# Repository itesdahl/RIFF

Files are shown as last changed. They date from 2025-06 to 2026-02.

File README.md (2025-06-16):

# The RIFF 600/900 DIY 3D printer
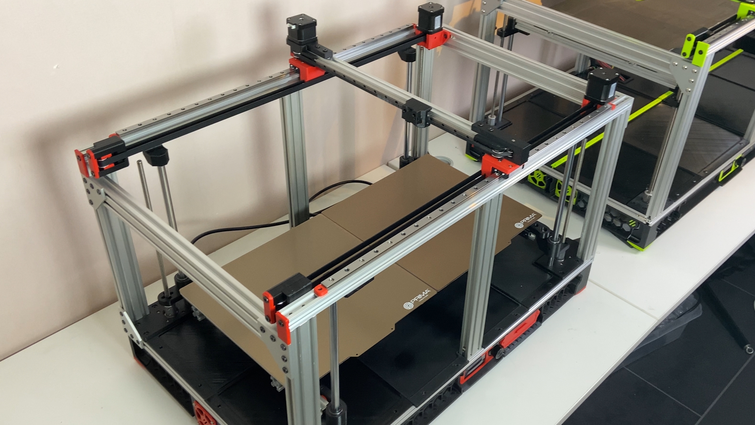
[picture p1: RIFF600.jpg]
CRIFF 600


You'll find the Youtube build series about the RIFF 600 here https://www.youtube.com/playlist?list=PLHk1C7nPAl80ZWU28OD7yWof3j6T3yG72  
You can also find the published STLs on: https://www.printables.com/model/1291703-the-riff-large-3d-printer

This is a 300x600 (RIFF 600) or 300x900 (RIFF 900) size DIY printer that can be built without spending a fortune. 

I encourage the use of second hand parts and will not provide any complete BOM (listing specific new components/brands). 

The prototype/PoC for the RIFF series is the LemonBreeze. That printer is not as space efficient as the RIFF printers: https://www.youtube.com/playlist?list=PLHk1C7nPAl83ME56pqZpkaPyZSMLXAlih

> [!NOTE]
> Future plans for this project is to add the Bondtech Indx. It should be a good fit for this frame, for printing signs etc..

## Some key information about my original RIFF 600 build:

- Build plate 300 x 600 (assembly with 2 pcs 300x300 heat beds in the RIFF 600, 3 pcs in the RIFF 900) 
- 2020 and 2040 extrusions 
- SKR 1.4 turbo and SKR Pico controllerboards (use whatever you have that have enough drivers and can run Klipper)
- Radxa Rock 3C SBC (or a Pi. SBC with 3-4 USB ports recommended)
- MGN 12H rails/carriage on Y and X. (350mm on X and 2x650 RIFF 600 or 2x950mm RIFF 900 on Y)
- 12mm rods and bearings on Z 
- Cartesian (the belts are a bit too long for corexy) 
- Klipper firmware 
- Dual Y steppermotors
- Sensorless homing on X and Y 
- Dragonburner with Sherpa micro 
- 2 x 360W 24V power supplies (3 x 360 24V in the 900 version)

## Video part 1:

### Cutting extrusions 600/900:

- 4x2020 775mm for Y (or 1075mm for the 900 version)
- 2x2020 450mm and 2x2040 450mm for X
- 6x2040 340mm for Z (or optionally 370mm)

### Blind joints and corner plates plates:

Tap M5 holes in all 6 2040 Z extrusions (or minimum 4 of them as shown in the video)
Tap M5 holes in the top Y extrusion at least in one end. (The one facing the rear of the printer) 
Optional but recommended, tap Y-extrusions in both ends to provide for two extra sets of corner plates and a couple of cover plates
Drill access holes in all Y-extrusions to get to the button head screws in the Z-extrusions
Attach the front and rear corner plates. The front 2040 x extrusion should sit 40mm below the top of the Y-extrusion

>[!TIP]
>Check the frame for squareness and adjust/correct  as needed.
>Mount the 4 z-motor mounts with M5 10mm bolts. The motor mounts makes the frame more rigid. Check the frame again for squareness.

# Video part 2
Parts for the front and rear arms (heat bed sub assembly): 

- Front 1x366mm 2020 extrusion and 2x625 bearings

- Rear 1x322mm 2020 extrusion

# Video part 3
- The 2020 extrusion for the x axis is 440mm

> [!CAUTION]
> On my 600 build the 2020 extrusions for the bed assembly is 2 pcs 645mm. You have to check the bed mounts on your heat bed to determine if you need longer extrusions.

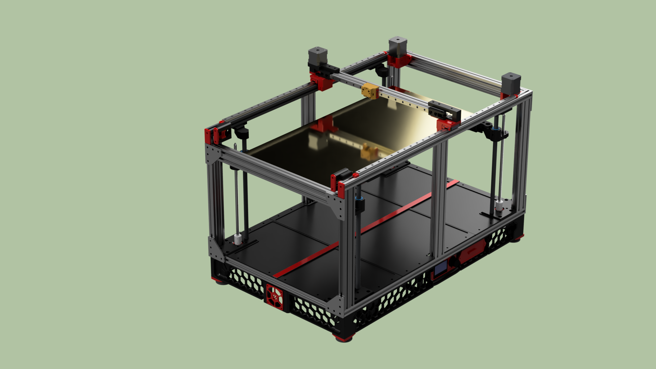
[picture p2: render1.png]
CAD model


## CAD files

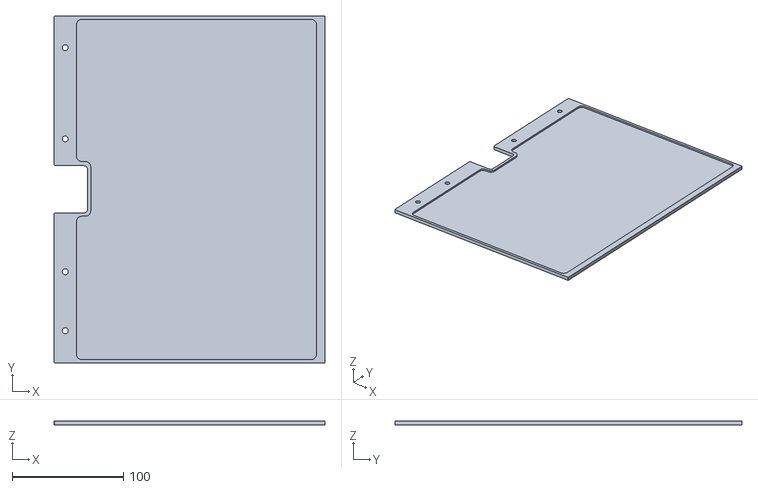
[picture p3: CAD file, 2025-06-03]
covers_skirt/mid_cover_left.stl
243.5 x 312.0 x 3.90

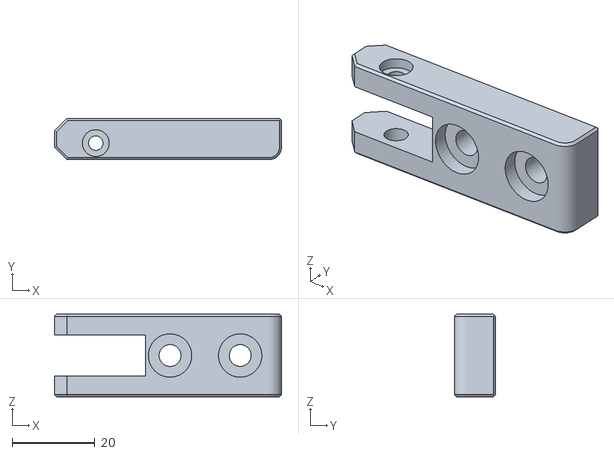
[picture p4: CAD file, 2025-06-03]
gantry/xoffset_motorside.stl
55.0 x 10.0 x 20.0

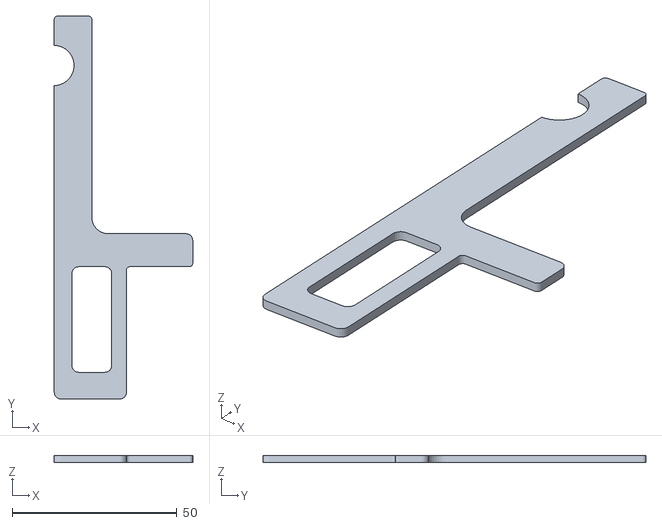
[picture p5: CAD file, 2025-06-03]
tools/jig_zrod_distance.stl
42.0 x 116.1 x 2.00

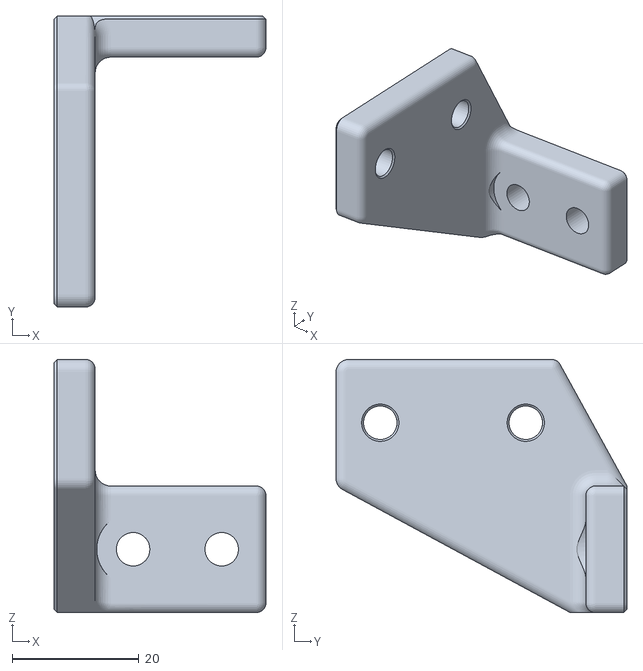
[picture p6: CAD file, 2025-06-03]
zaxis/2xbedbracketB.stl
33.5 x 46.0 x 40.0

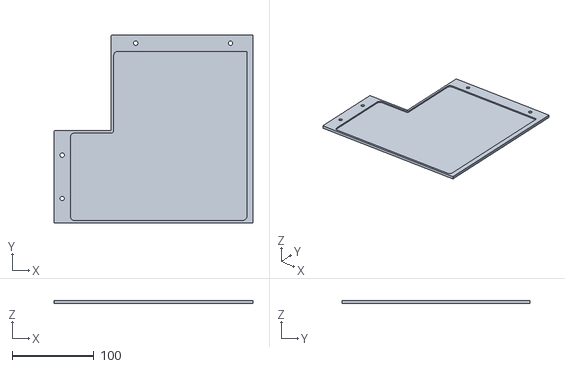
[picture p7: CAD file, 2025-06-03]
covers_skirt/rear_cover_left.stl
243.5 x 230.0 x 4.00

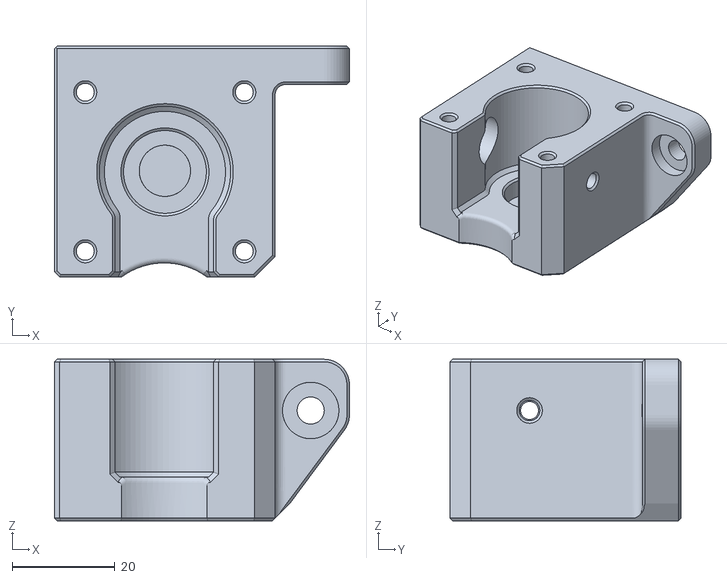
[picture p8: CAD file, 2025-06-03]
gantry/ymotor_mount_left.stl
57.5 x 45.0 x 31.5

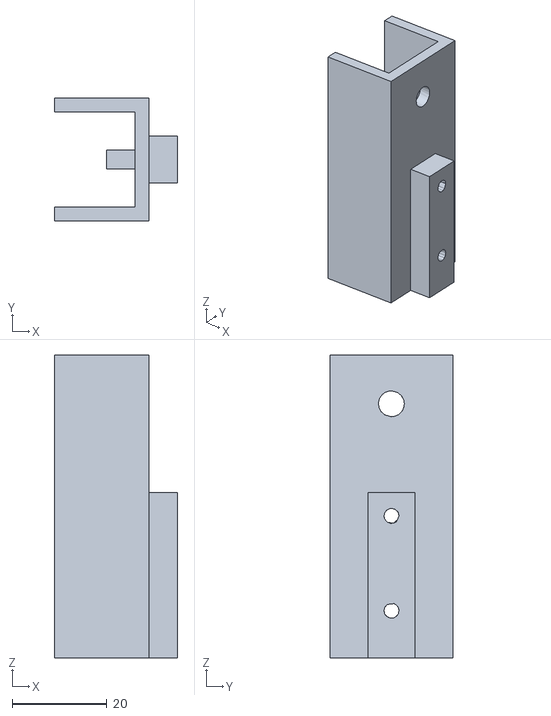
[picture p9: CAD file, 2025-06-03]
tools/jig_pilotholes.stl
26.0 x 26.0 x 64.0

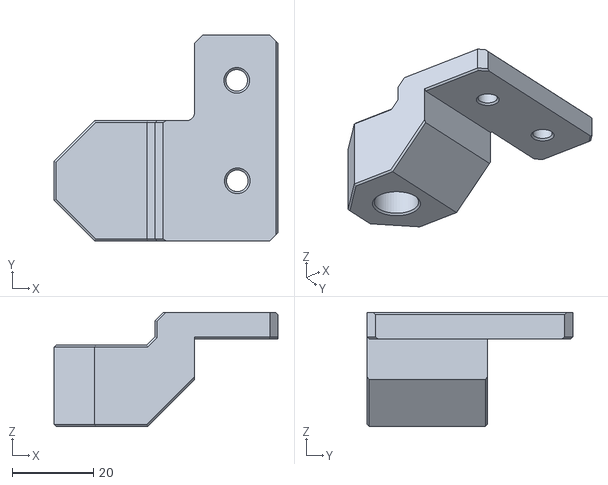
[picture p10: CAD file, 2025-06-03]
zaxis/2xzrod_mountA.stl
55.0 x 50.5 x 28.0

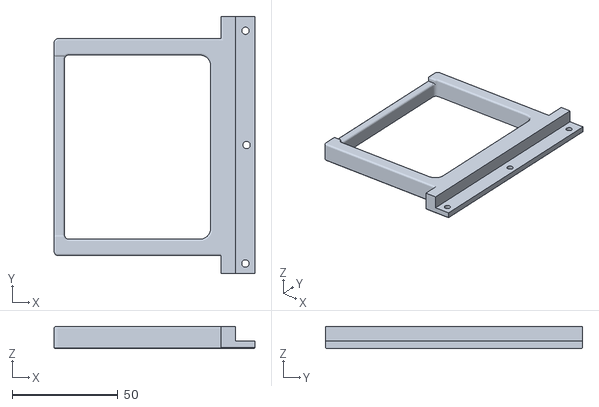
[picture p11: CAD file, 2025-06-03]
covers_skirt/caddy_supportbracket.stl
95.0 x 121.6 x 10.5

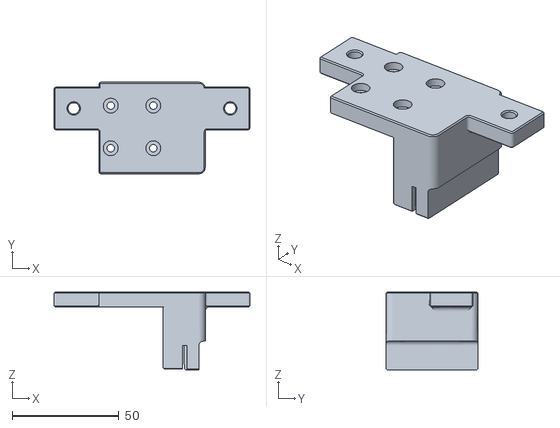
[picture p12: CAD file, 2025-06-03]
gantry/xyjoiner_left.stl
92.0 x 43.0 x 36.5

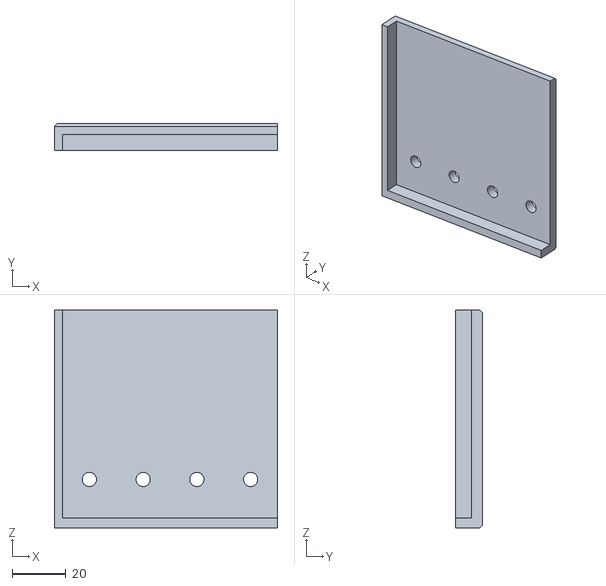
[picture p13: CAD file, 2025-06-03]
tools/jig_linup_extrusions.stl
83.0 x 10.0 x 81.0

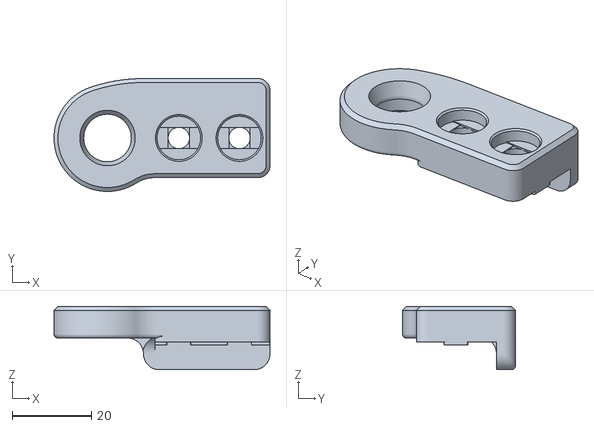
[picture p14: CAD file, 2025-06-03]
zaxis/left_spherical_left.stl
54.5 x 28.5 x 16.0

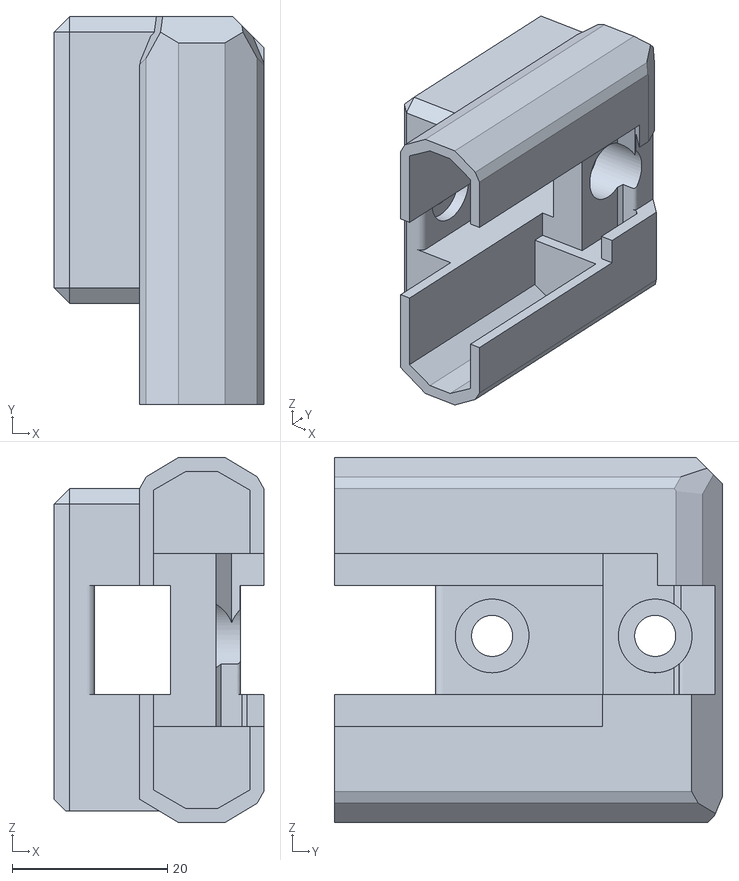
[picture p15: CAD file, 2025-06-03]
gantry/bfi_housing_left.stl
27.0 x 50.0 x 47.0

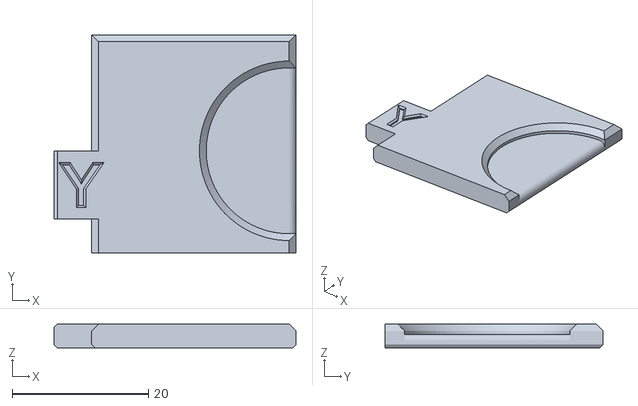
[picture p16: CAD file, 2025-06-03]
tools/jig_y_pulley.stl
35.5 x 32.0 x 3.50

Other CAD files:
covers_skirt/front_cover_left.stl
zaxis/2xspacer_front_bedarm.stl
covers_skirt/caddy_SKR14_13.stl
gantry/xoffset_idlerside.stl
covers_skirt/4xbridge.stl
covers_skirt/4xfeet_tpu.stl
covers_skirt/caddy_frame.stl
covers_skirt/front_cover_right.stl
covers_skirt/mid_cover_right.stl
covers_skirt/rear_cover_right.stl
gantry/bfi_frontcover_left.stl
gantry/bfi_frontcover_right.stl
gantry/bfi_housing_right.stl
gantry/bfi_idler_holder_left.stl
gantry/bfi_idler_holder_right.stl
gantry/xidler_mount.stl
gantry/xmotor_mount.stl
gantry/xyjoiner_right.stl
gantry/ymotor_mount_right.stl
tools/jig_x_pulley.stl
zaxis/2x_zmotor_A.stl
zaxis/2x_zmotor_B.stl
zaxis/2xbedbracketA.stl
zaxis/2xzrod_mountB.stl
zaxis/4xadapter_ring.stl
zaxis/front_bedarm_left.stl
zaxis/front_bedarm_right.stl
zaxis/front_clamp_left.stl
zaxis/front_clamp_right.stl
zaxis/rear_bedarm_left.stl
zaxis/rear_bedarm_right.stl
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

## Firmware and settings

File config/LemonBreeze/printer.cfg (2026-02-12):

[include mainsail.cfg]

[mcu]
serial: /dev/serial/by-id/usb-Klipper_ 
[mcu xy]
serial: /dev/serial/by-id/usb-Klipper_ 

[printer]
kinematics: cartesian
max_velocity: 250  
max_accel: 4000
max_z_velocity: 3
max_z_accel: 50
square_corner_velocity: 5.0

[virtual_sdcard]
path: /home/radxa/printer_data/gcodes

on_error_gcode: CANCEL_PRINT

[gcode_arcs]
[exclude_object]
[force_move]
enable_force_move: True

[include homing.cfg]
[include stealthburner_leds.cfg]
[include clean_nozzle.cfg]
#[include PIS.cfg]

[input_shaper]
shaper_type_x = mzv
shaper_freq_x = 69.0
shaper_type_y = 2hump_ei
shaper_freq_y = 60.2

[stepper_x]
step_pin: xy:gpio11
dir_pin: xy:gpio10
enable_pin: !xy:gpio12
microsteps: 16
rotation_distance: 40
full_steps_per_rotation: 200
endstop_pin: tmc2209_stepper_x:virtual_endstop
#endstop_pin: ^gpio4
position_endstop: 300
position_min: 0
position_max: 300
homing_speed: 50
homing_retract_dist: 0
homing_positive_dir: true

[tmc2209 stepper_x]
uart_pin: xy:gpio9
tx_pin: xy:gpio8
uart_address: 0
run_current: 0.650
stealthchop_threshold: 0
diag_pin: ^xy:gpio4
driver_SGTHRS: 85

[stepper_y]
step_pin: xy:gpio6
dir_pin: xy:gpio5
enable_pin: !xy:gpio7
microsteps: 16
rotation_distance: 40
full_steps_per_rotation: 200
endstop_pin: tmc2209_stepper_y:virtual_endstop
#endstop_pin: ^gpio3
position_endstop: 813
position_max: 813
position_min: 0
homing_speed: 50
homing_retract_dist: 0
homing_positive_dir: true

[tmc2209 stepper_y]
uart_pin: xy:gpio9
tx_pin: xy:gpio8
uart_address: 2
run_current: 0.800
stealthchop_threshold: 0
diag_pin: ^xy:gpio3
driver_SGTHRS: 65

[stepper_y1]
step_pin: xy:gpio19
dir_pin: !xy:gpio28
enable_pin: !xy:gpio2
microsteps: 16
rotation_distance: 40
full_steps_per_rotation: 200


[tmc2209 stepper_y1]
uart_pin: xy:gpio9
tx_pin: xy:gpio8
uart_address: 1
run_current: 0.800
stealthchop_threshold: 0


[extruder]
step_pin: xy:gpio14
dir_pin: !xy:gpio13
enable_pin: !xy:gpio15
microsteps: 16
rotation_distance: 22.6789511   #Bondtech 5mm Drive Gears
gear_ratio: 50:10
microsteps: 16
full_steps_per_rotation: 200
nozzle_diameter: 0.800
filament_diameter: 1.750
min_temp: 10
max_temp: 280
max_power: 0.8
min_extrude_temp: 170
heater_pin: xy:gpio23
sensor_type: Generic 3950
sensor_pin: xy:gpio27
control = pid
pid_kp = 34.855
pid_ki = 11.619
pid_kd = 26.141
min_temp: 0
max_temp: 280

[tmc2209 extruder]
uart_pin: xy:gpio9
tx_pin: xy:gpio8
uart_address: 3
run_current: 0.500
stealthchop_threshold: 0

[fan]
pin: xy:gpio18

[heater_fan heatbreak_cooling_fan]
pin: xy:gpio17

[heater_fan controller_fan]
pin: xy:gpio20


[stepper_z]
step_pin: P2.2
dir_pin: !P2.6
enable_pin: !P2.1
rotation_distance: 8
microsteps: 16
endstop_pin: probe:z_virtual_endstop
#endstop_pin: P1.27
#position_endstop: -0.5
position_min: -5
homing_speed: 8
second_homing_speed: 3
homing_retract_dist: 3
position_max: 240
position_min: -5
homing_speed: 8
second_homing_speed: 3
homing_retract_dist: 3

[probe]
pin: xy:gpio22
x_offset: 0
y_offset: 25
z_offset: 4.45
samples: 3
samples_result: median
sample_retract_dist: 3
samples_tolerance: 0.055
samples_tolerance_retries: 3

[tmc2209 stepper_z]
uart_pin: P1.10
interpolate: False
run_current: 0.65
sense_resistor: 0.110
stealthchop_threshold: 0

[stepper_z1]
step_pin: P0.19
dir_pin: !P0.20
enable_pin: !P2.8
rotation_distance: 8
microsteps: 16

[tmc2209 stepper_z1]
uart_pin: P1.9
interpolate: False
run_current: 0.65
sense_resistor: 0.110
stealthchop_threshold: 0


[stepper_z2]
step_pin: P0.22
dir_pin: P2.11
enable_pin: !P0.21
rotation_distance: 8
microsteps: 16

[tmc2209 stepper_z2]
uart_pin: P1.8
interpolate: False
run_current: 0.65
sense_resistor: 0.110
stealthchop_threshold: 0

[stepper_z3]
step_pin: P2.13
dir_pin: !P0.11
enable_pin: !P2.12
rotation_distance: 8
microsteps: 16

[tmc2209 stepper_z3]
uart_pin: P1.4
interpolate: False
run_current: 0.65
sense_resistor: 0.110
stealthchop_threshold: 0


[z_tilt]
##  Use Z_TILT_ADJUST to level the bed
z_positions:
	-85,70
    -85,855
    380,855
    380,70
points:
	30,30
    150, 750
	270,30

speed:100
horizontal_move_z: 15
retries: 5
retry_tolerance: 1.1

[bed_mesh]
speed: 120
horizontal_move_z: 5.5
mesh_min: 30, 30
mesh_max: 200, 750 
probe_count: 6, 21
mesh_pps: 2, 2
algorithm: bicubic
bicubic_tension: 0.2


[heater_bed]
heater_pin: xy:gpio21
sensor_type: EPCOS 100K B57560G104F
sensor_pin: xy:gpio26
control: pid
pid_kp = 69.604
pid_ki = 1.278
pid_kd = 947.440
min_temp: 0
max_temp: 90

[heater_generic heater_bed_2]
heater_pin: P2.5
sensor_type: EPCOS 100K B57560G104F
sensor_pin: P0.25
control: pid
pid_kp = 69.725
pid_ki = 1.375
pid_kd = 883.762
min_temp: 0
max_temp: 90


[heater_generic heater_bed_3]
heater_pin: P2.7
sensor_type: EPCOS 100K B57560G104F
sensor_pin: P0.24
control: pid
pid_kp = 68.044
pid_ki = 1.243
pid_kd = 931.355
min_temp: 0
max_temp: 90



########################################
# EXP1 / EXP2 (display) pins
########################################

[board_pins]
aliases:
    # EXP1 header
    EXP1_1=P1.30, EXP1_3=P1.18, EXP1_5=P1.20, EXP1_7=P1.22, EXP1_9=<GND>,
    EXP1_2=P0.28, EXP1_4=P1.19, EXP1_6=P1.21, EXP1_8=P1.23, EXP1_10=<5V>,
    # EXP2 header
    EXP2_1=P0.17, EXP2_3=P3.26, EXP2_5=P3.25, EXP2_7=P1.31, EXP2_9=<GND>,
    EXP2_2=P0.15, EXP2_4=P0.16, EXP2_6=P0.18, EXP2_8=<RST>, EXP2_10=<NC>
    # Pins EXP2_1, EXP2_6, EXP2_2 are also MISO, MOSI, SCK of bus "ssp0"

##  mini12864 LCD Display
[display]
lcd_type: uc1701
cs_pin: P1.18
a0_pin: P1.19
encoder_pins: ^P3.26,^P3.25
click_pin: ^!P0.28
contrast: 63

##  To control Neopixel RGB in mini12864 display
[neopixel fysetc_mini12864]
pin: P1.21
chain_count: 3
initial_RED: 0.1
initial_GREEN: 0.5
initial_BLUE: 0.0
color_order: RGB

##  Set RGB values on boot up for each Neopixel. 
##  Index 1 = display, Index 2 and 3 = Knob
[delayed_gcode setdisplayneopixel]
initial_duration: 1
gcode:
       SET_LED LED=fysetc_mini12864 RED=1 GREEN=1 BLUE=1 INDEX=1 TRANSMIT=0
       SET_LED LED=fysetc_mini12864 RED=1 GREEN=0 BLUE=0 INDEX=2 TRANSMIT=0
       SET_LED LED=fysetc_mini12864 RED=1 GREEN=0 BLUE=0 INDEX=3 


# See the sample-lcd.cfg file for definitions of common LCD displays.

#macros from here

[gcode_macro _HOME_X]
gcode:
    # Always use consistent run_current on A/B steppers during sensorless homing
    {% set RUN_CURRENT_X = printer.configfile.settings['tmc2209 stepper_x'].run_current|float %}
    {% set RUN_CURRENT_Y = printer.configfile.settings['tmc2209 stepper_y'].run_current|float %}
     {% set RUN_CURRENT_Y = printer.configfile.settings['tmc2209 stepper_y1'].run_current|float %}
    {% set HOME_CURRENT = 0.7 %}
    SET_TMC_CURRENT STEPPER=stepper_x CURRENT={HOME_CURRENT}
    SET_TMC_CURRENT STEPPER=stepper_y CURRENT={HOME_CURRENT}
    SET_TMC_CURRENT STEPPER=stepper_y1 CURRENT={HOME_CURRENT}

    # Home
    G28 X
    # Move away
    G91
    G1 X-10 F1200
    
    # Wait just a second… (give StallGuard registers time to clear)
    G4 P1000
    # Set current during print
    SET_TMC_CURRENT STEPPER=stepper_x CURRENT={RUN_CURRENT_X}
    SET_TMC_CURRENT STEPPER=stepper_y CURRENT={RUN_CURRENT_Y}
     SET_TMC_CURRENT STEPPER=stepper_y1 CURRENT={RUN_CURRENT_Y}

[gcode_macro _HOME_Y]
gcode:
    # Set current for sensorless homing
    {% set RUN_CURRENT_X = printer.configfile.settings['tmc2209 stepper_x'].run_current|float %}
    {% set RUN_CURRENT_Y = printer.configfile.settings['tmc2209 stepper_y'].run_current|float %}
    {% set RUN_CURRENT_Y = printer.configfile.settings['tmc2209 stepper_y1'].run_current|float %}
    {% set HOME_CURRENT = 0.7 %}
    SET_TMC_CURRENT STEPPER=stepper_x CURRENT={HOME_CURRENT}
    SET_TMC_CURRENT STEPPER=stepper_y CURRENT={HOME_CURRENT}
    SET_TMC_CURRENT STEPPER=stepper_y1 CURRENT={HOME_CURRENT}

    # Home
    G28 Y
    # Move away
    G91
    G1 Y-10 F1200

    # Wait just a second… (give StallGuard registers time to clear)
    G4 P1000
    # Set current during print
    SET_TMC_CURRENT STEPPER=stepper_x CURRENT={RUN_CURRENT_X}
    SET_TMC_CURRENT STEPPER=stepper_y CURRENT={RUN_CURRENT_Y}
    SET_TMC_CURRENT STEPPER=stepper_y1 CURRENT={RUN_CURRENT_Y}
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

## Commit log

2025-06-03 Intitial version of the CAD model
    [2x_zmotor_A.stl, 2x_zmotor_B.stl, 2xbedbracketA.stl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]
2025-06-03 Changed the mid left cover
    Changed the mid left cover to make room for heatbed cables
2025-08-02 Create RIFF 600 v168.zip
    Added a basic bate plate for the xy controller
2025-08-04 Delete RIFF 600 v168.zip
    Outdated Pico mount
2026-02-12 Changed to 3 probe points
    [printer.cfg]
